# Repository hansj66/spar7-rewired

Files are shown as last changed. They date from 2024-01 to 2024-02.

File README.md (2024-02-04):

# Spar7 Rewired

This repository contains schematics, PCB layout, gerber files and STEP/STL files necessary for a complete Spar 7 rebuild.

 > **Disclaimer:** This repository contains information about my own rebuild. I can not guarantee that this will work as expected in YOUR game. It is entirely possible that you will break your beautiful collector quality game beyond repair trying to retrofit this board and the 3D printed hopper mechanism. Proceed at your own risk :)

Note: The payout slide is currently made of 1.7mm thick 3D printed plastic. This part will wear out over time, and the life expectancy of this part is currently unknown. A CNC fabricated aluminium/steel sheet with 3D printed endcaps is a better option if this is a concern.

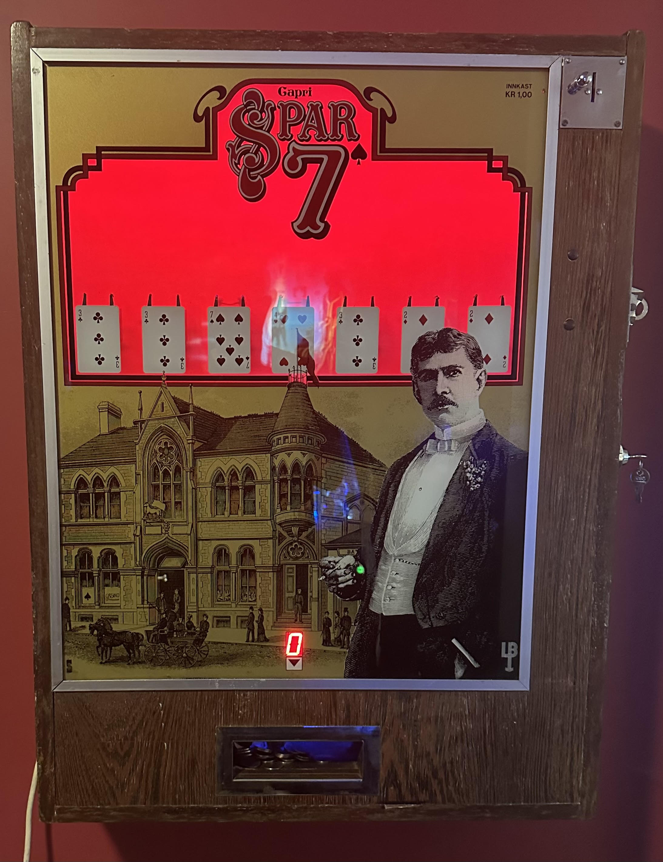
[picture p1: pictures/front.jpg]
Spar7

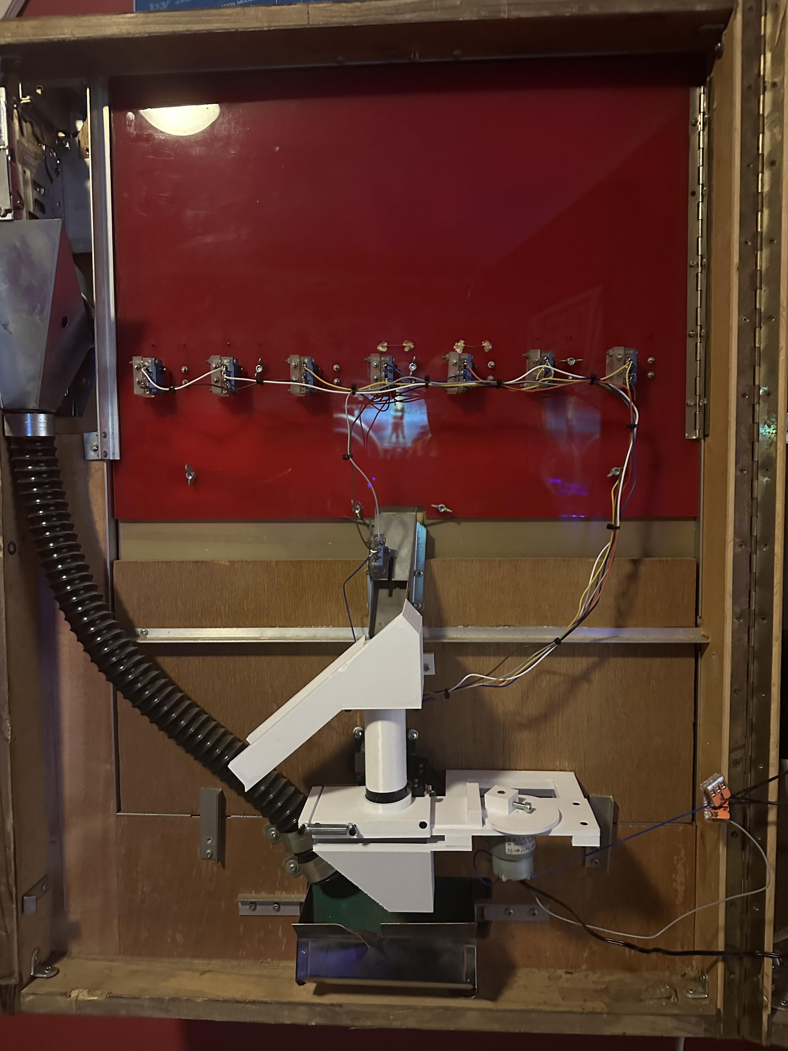
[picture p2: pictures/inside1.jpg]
Spar7_2

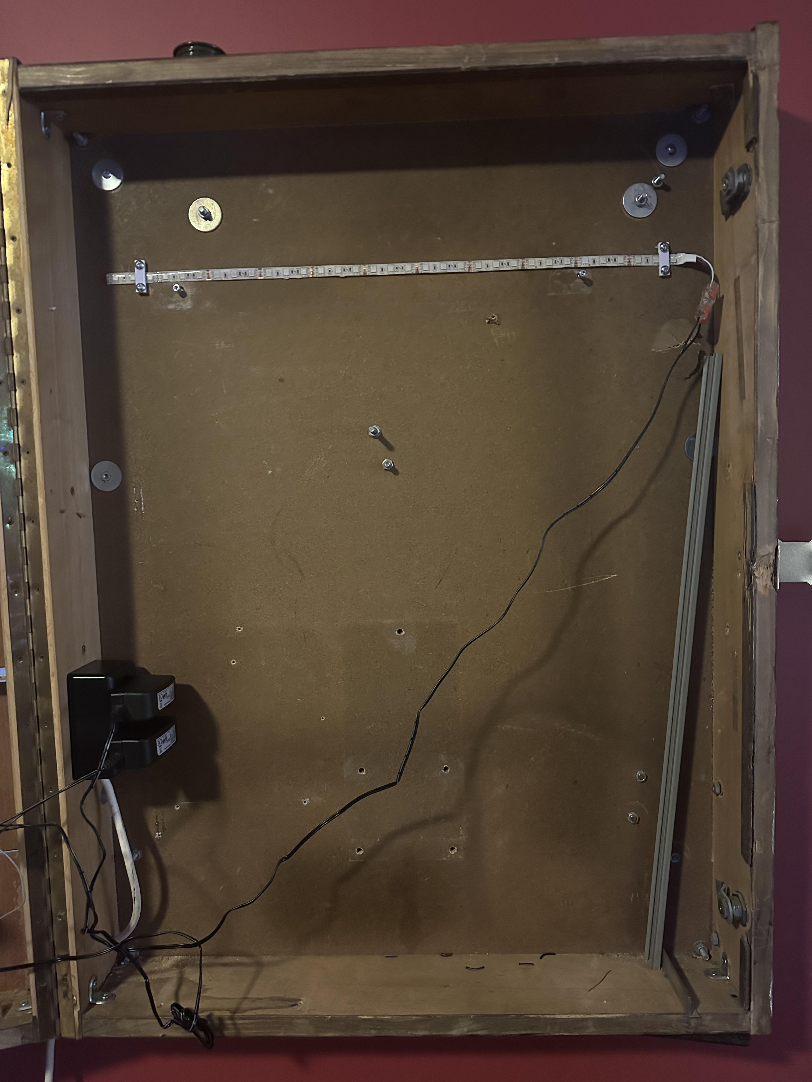
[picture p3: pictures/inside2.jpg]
Spar7_3


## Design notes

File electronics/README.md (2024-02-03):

# Eagle files

Here you will find a bill of materials along with eagle project files. Gerber files that can be uploaded to a PCB manufacturer can be found in the CAM folder

## Notes
1. There is no hardware debouncing in this version. A RC filter + schmitt trigger should be added to the inputs if you are planing on using interrupt handlers for the inputs.
2. The relay is rated for higher voltages than 12V, but I would not recommend using this for controlling a line voltage driven AC motor (220V can kill).
3. The 3.3V, 12V and USB leds are a bit on the bright side. Use series resistors with a higher resistance or consider not mounting these LEDs if light leakage to the payout slot is considered annoying.

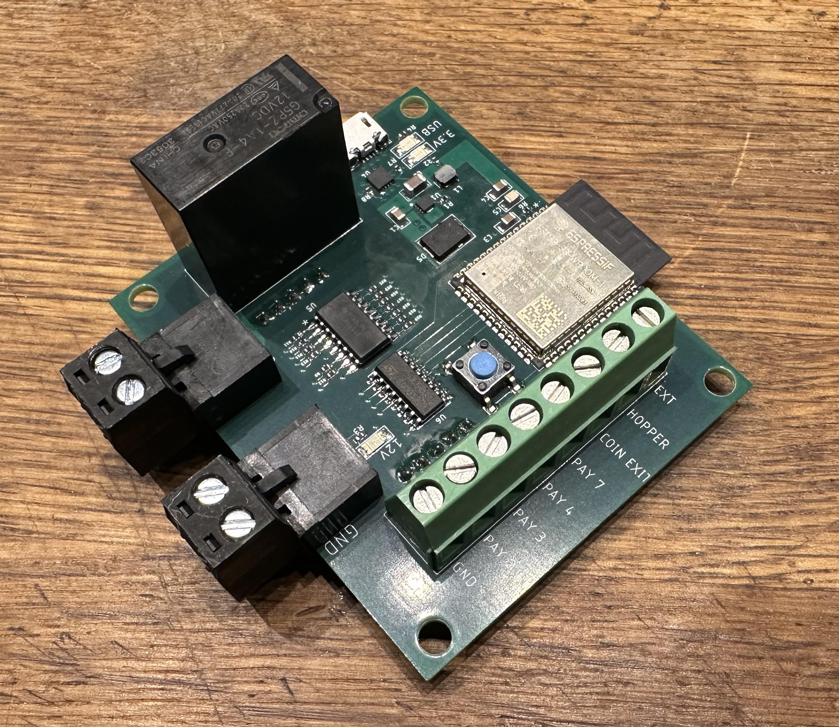
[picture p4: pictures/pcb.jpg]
pcb


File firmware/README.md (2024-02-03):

# Spar 7 Controller

## Building the firmware

1. Download [espressif installer ](https://dl.espressif.com/dl/esp-idf/?idf=4.4)
2. Configure environemnt variable IDF_PATH to point to espressif installation folder
3. If using visual studio code: Install the espressif plugin
4. Drop any certs into the certs/ folder. Any files dropped here will be packed into spiffs.bin if you run the makespiffs.cmd script. The spiffs.bin file will in turn automatically be flashed to the spiffs partition when you flash the firmware. This is required if you want to communicate using dtls over the wifi network.

```
idf.py build 
```

## Flashing

The board can be flashed using a USB Micro B cable. Press the blue button and apply power to the board to enter bootloader mode.

```
idf.py flash -p <port>
```

## Logging / shell

Log output and shell commands are available via USB. Type "Help" to get a list of commands.

```
idf.py monitor
```

## Shell commands

| Command  | Description |
| --- | --- |
| help  | Print the list of registered commands.  |
| free  | Get the current size of free heap memory.  |
| heap  | Get minimum size of free heap memory that was available during program execution.|
| version  | Get version of chip, SDK and firmware.  |
| restart | Software reset of the chip. |
| tasks  | Get information about running tasks. |
| log_level  \<tag\|\*\> \<none\|error\|warn\|debug\|verbose\>  |  Set log level for all tags or a specific tag. |
| get_delays  | Get information about current debounce / delay settings. |
| set_delay  <hopper\|exit\|payout> \<ms\>  |  Set debounce delay for a switch group (hopper, coin exit or payout) in milliseconds.|
| set_wifi \<ssid\> \<password\>  |  Set wifi ssid/password for your local network. (required for backend functionality). |
| ip  |  Get IP address. |
| dir  |  Lists files in filesystem. |
| txtest  |  Sends a hello world message to the backend. |

## Necessary hardware changes.

* Remove the internal lighting, power supply, hopper, printed circuit boards and associated wiring.
* 3D print all STL files in the "3D-print\STL" folder and assemble the new hopper (You will also need an assortment of 6mm, 15mm and 20mm M3 screws and 4 wood screws). The hopper is designed for a 12V JBG37-520 geared DC motor (60 or 120 RPM). If a motor with a different form factor is going to be used, you will have to import, modify and reslice the step files accordingly.
* Replace the existing fluorescent tube with a 12V LED strip. This can be powered from the same power supply as the motor.

> Note: The 7 segment display is optional. The board will work fine for games that don't have display option.

### 1. Switch wiring
* Remove (or modify) the existing wiring harness. If the switch terminal lugs are heavily oxidized, it may be a good idea to solder the wiring harness directly to the lugs instead of using connectors.
* Route a common switch ground wire through all payout switches, coin exit switch and hopper switch and connect this to the GND terminal on the 8 pin terminal block.
* Route all wires from the "2"-switches to the ""Pay 2" terminal, "3"-switches to the "Pay 3" etc. Also connect the "coin exit" and hopper switches to the corresponding terminals (The "Ext" terminal is currently not in use)

### 2. Motor wiring
1. Connect a 12V 1A power supply to the power pluggable terminal block.
1.  Connect the motor in series with a separate 12V power supply and connect the remaining wire going from the power supply and the remaning wire going from the motor to the "Motor Relay" pluggable terminal block.
1. In case the default debounce delays don't work for your setup, these delays can be changed using shell commands (the shell is always available via the USB.)

Example:

Changing the hopper debounce delay to 250ms:
```
set_delay hopper 250
```
## IoT Backend Notes

If you are using the [https://span.lab5e.com/](https://span.lab5e.com/) IoT backend, you will have to create a representation of your device and download the necessary certificates. (It's free to register and use for hobbyists level number of devices and data. You'll find all necessary information in the [Getting Started section](https://www.lab5e.com/docs/get_started/) of the documentation).

1. Create a folder under firmware (firmware\certs) and drop the <deviceid>-cert.crt, the <deviceid>-key.key and the span-cert-chain.crt in this folder
1. Concatenate <deviceid>-cert.crt and span-cert-chain.crt to a new 'cert.crt' file in the same folder (the device cert has to be the first certificate).

This folder will automatically be flashed to the spiffs partition when you flash the firmware. If you set the wifi ssid and password using the command shell, the firmware will try to connect to your wifi. If successful, bookkeeping data will then be sent when coins are received or paid out from the game using dtls.

The protocol is rather simple. Messages consist of one byte only. A positive number == coin in. A negative number == coins out. (I considered using protobuffers, but decided it would be overkill for now...)

The Span backend provides data retention. It also has a REST api and various outputs that make it simple to write a small application/backend to retrieve these messages from Span at your convenience. [Example clients](https://www.lab5e.com/docs/backend/) are available for a wide variety of languages.

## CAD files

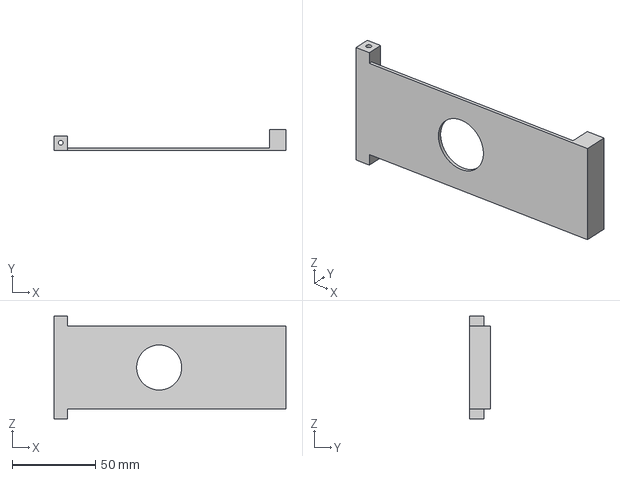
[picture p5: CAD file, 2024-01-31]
3D_print/step/slider.step
139.0 x 12.7 x 61.4 mm

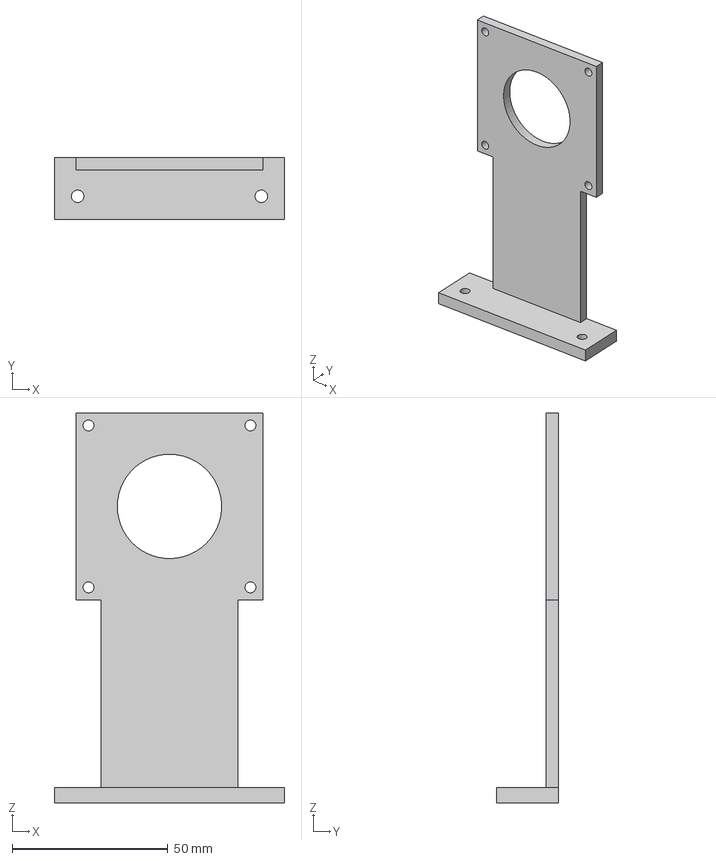
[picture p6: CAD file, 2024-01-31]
3D_print/step/tube bracket.step
74.0 x 20.0 x 125.2 mm

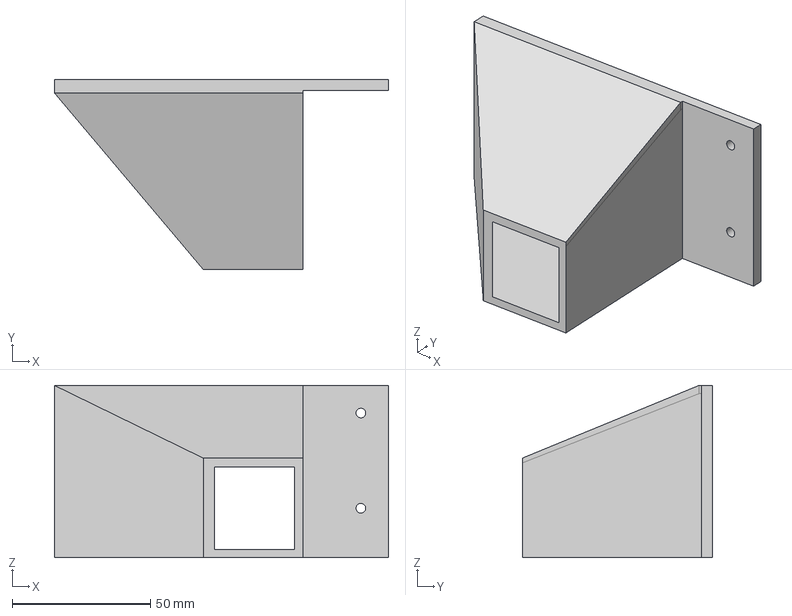
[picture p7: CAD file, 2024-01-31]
3D_print/step/funnel.step
121.0 x 69.0 x 62.3 mm

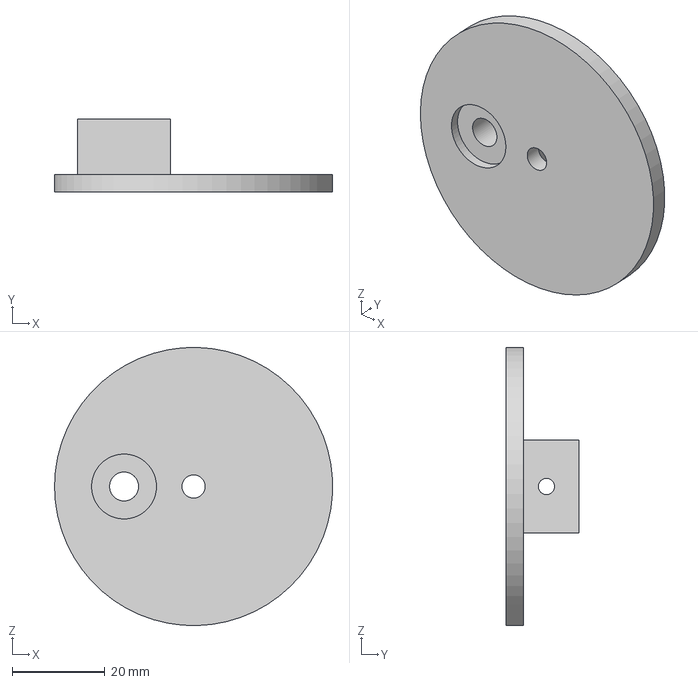
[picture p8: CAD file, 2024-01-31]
3D_print/step/rotor.step
60.0 x 15.7 x 60.0 mm

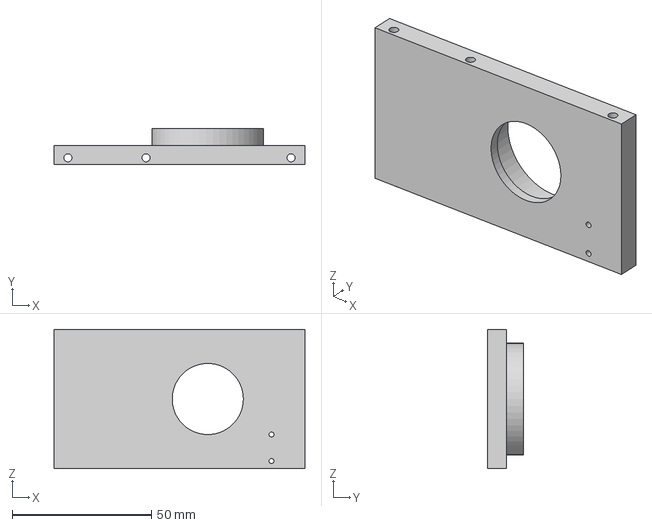
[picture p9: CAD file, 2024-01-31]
3D_print/step/top plate.step
90.0 x 12.9 x 50.0 mm

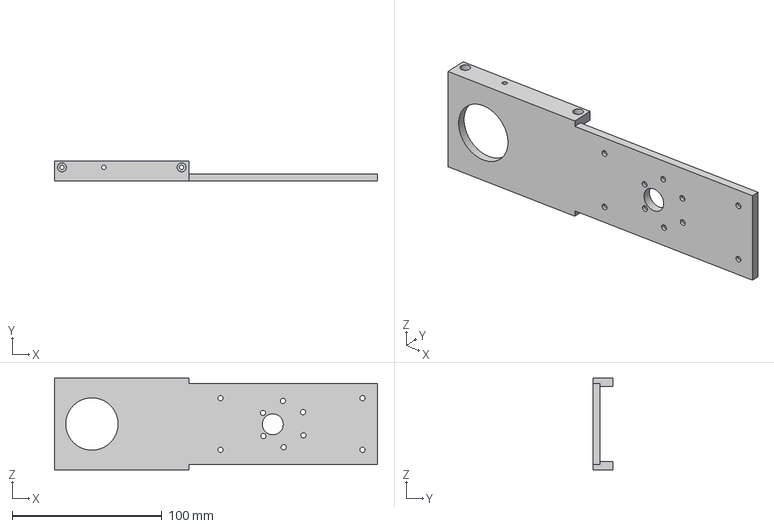
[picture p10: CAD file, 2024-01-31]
3D_print/step/bottom_plate.step
216.0 x 13.7 x 61.5 mm

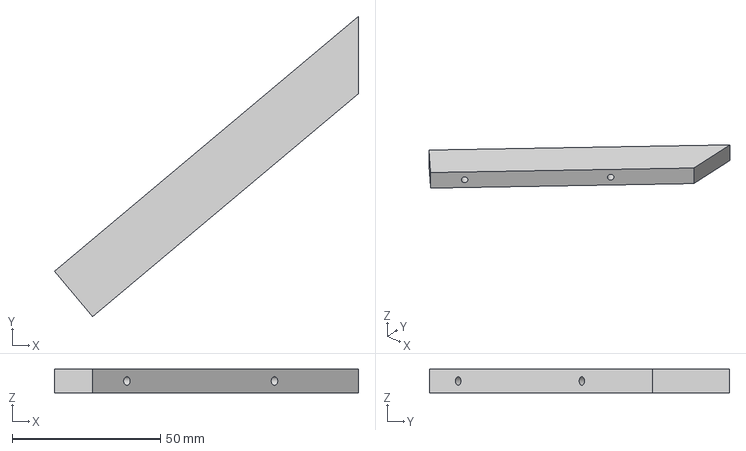
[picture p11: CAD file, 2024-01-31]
3D_print/step/coin chute_b.step
102.6 x 101.4 x 8.00 mm

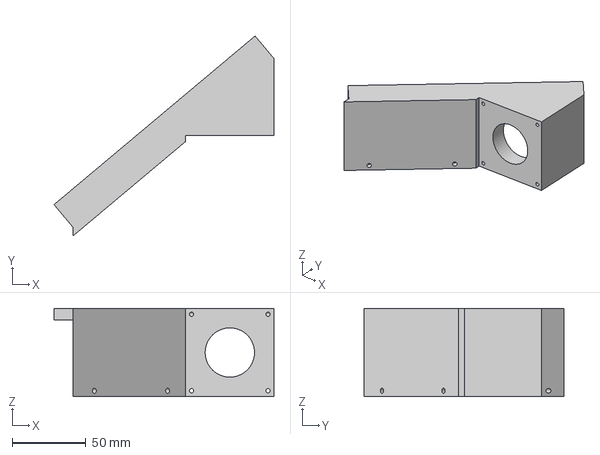
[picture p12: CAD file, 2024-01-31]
3D_print/step/coin chute_a.step
149.5 x 135.9 x 60.0 mm

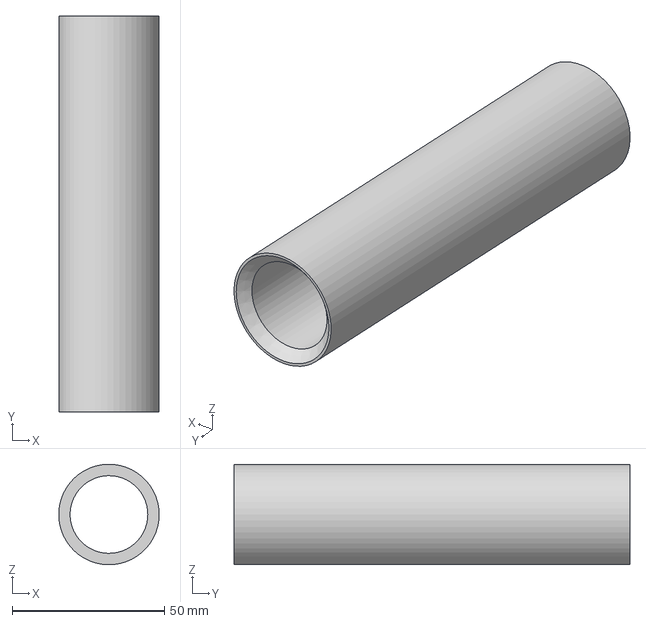
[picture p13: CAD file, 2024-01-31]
3D_print/step/coin tube.step
33.0 x 130.0 x 33.0 mm

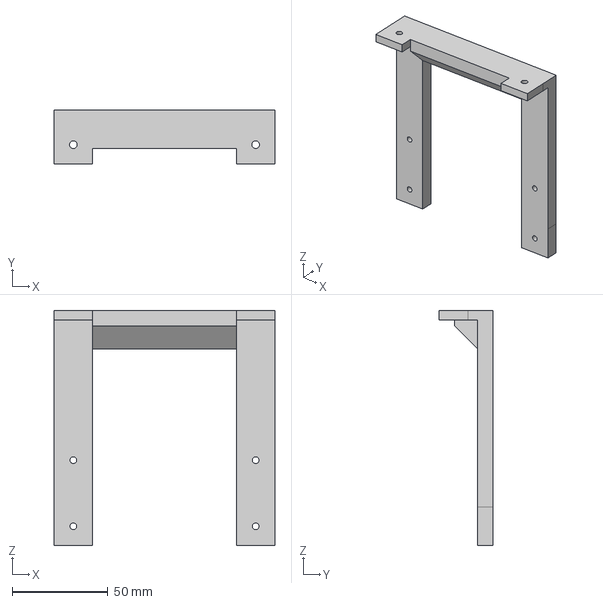
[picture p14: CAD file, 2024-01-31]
3D_print/step/bracket.step
115.0 x 28.0 x 122.5 mm

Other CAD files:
3D_print/fusion360/Hopper - Alternative version v18.f3d
3D_print/stl/Coin Tube.stl
3D_print/stl/Top plate.stl
3D_print/stl/Tube bracket.stl
3D_print/stl/bottom_plate.stl
3D_print/stl/bracket.stl
3D_print/stl/coin chute_a.stl
3D_print/stl/coin chute_b.stl
3D_print/stl/funnel.stl
3D_print/stl/rotor.stl
3D_print/stl/slider.stl

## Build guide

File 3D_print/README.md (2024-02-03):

# Spar 7 Alternative Hopper

Here you will find STL files for 3D printing the alternative hopper. STEP-files and a Fusion360 project export are also included (in case you would like to modify the design)

## Notes
1. 4 wooden screws are needed to mount the hopper to the inside plywood wall. Make sure to use short screws, so you don't penetrate the plywood and break the front glass ;)
2. The CAM is for a 6mm shaft motor. It is secured to the shaft using an M4 screw
3. Assembling thw hopper requires M3 6mm screws, M3 15 and 20mm screws
4. The payout slide requires two soft springs (approx 20mm in length)
5. The motor bracket is designed for a JGB37-500 motor. This can be sourced from AliExpress.

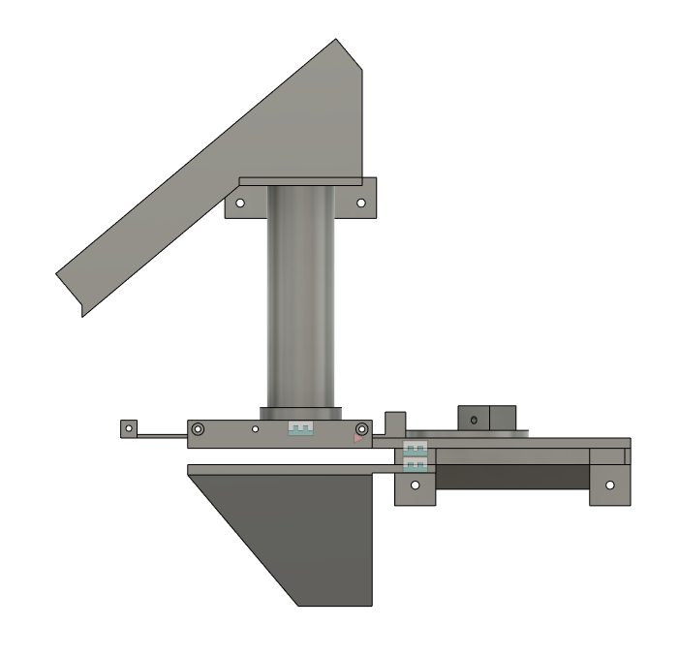
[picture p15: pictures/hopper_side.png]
hopper side

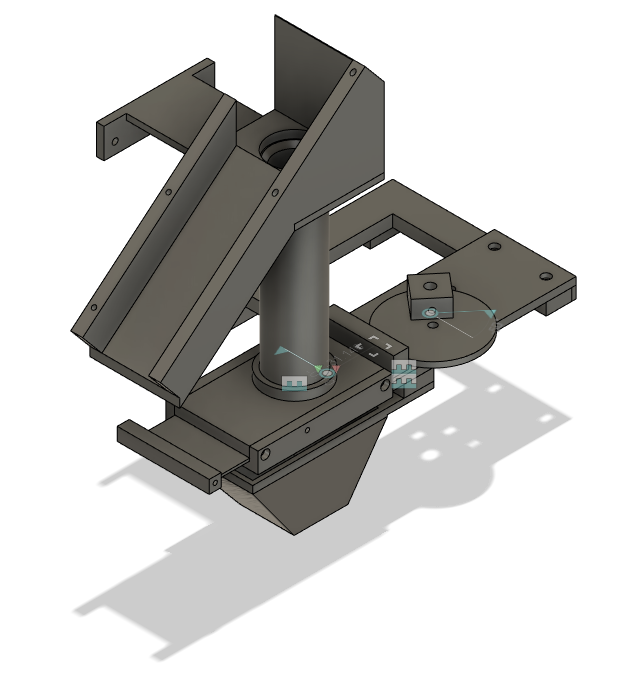
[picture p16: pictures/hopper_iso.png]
hopper iso


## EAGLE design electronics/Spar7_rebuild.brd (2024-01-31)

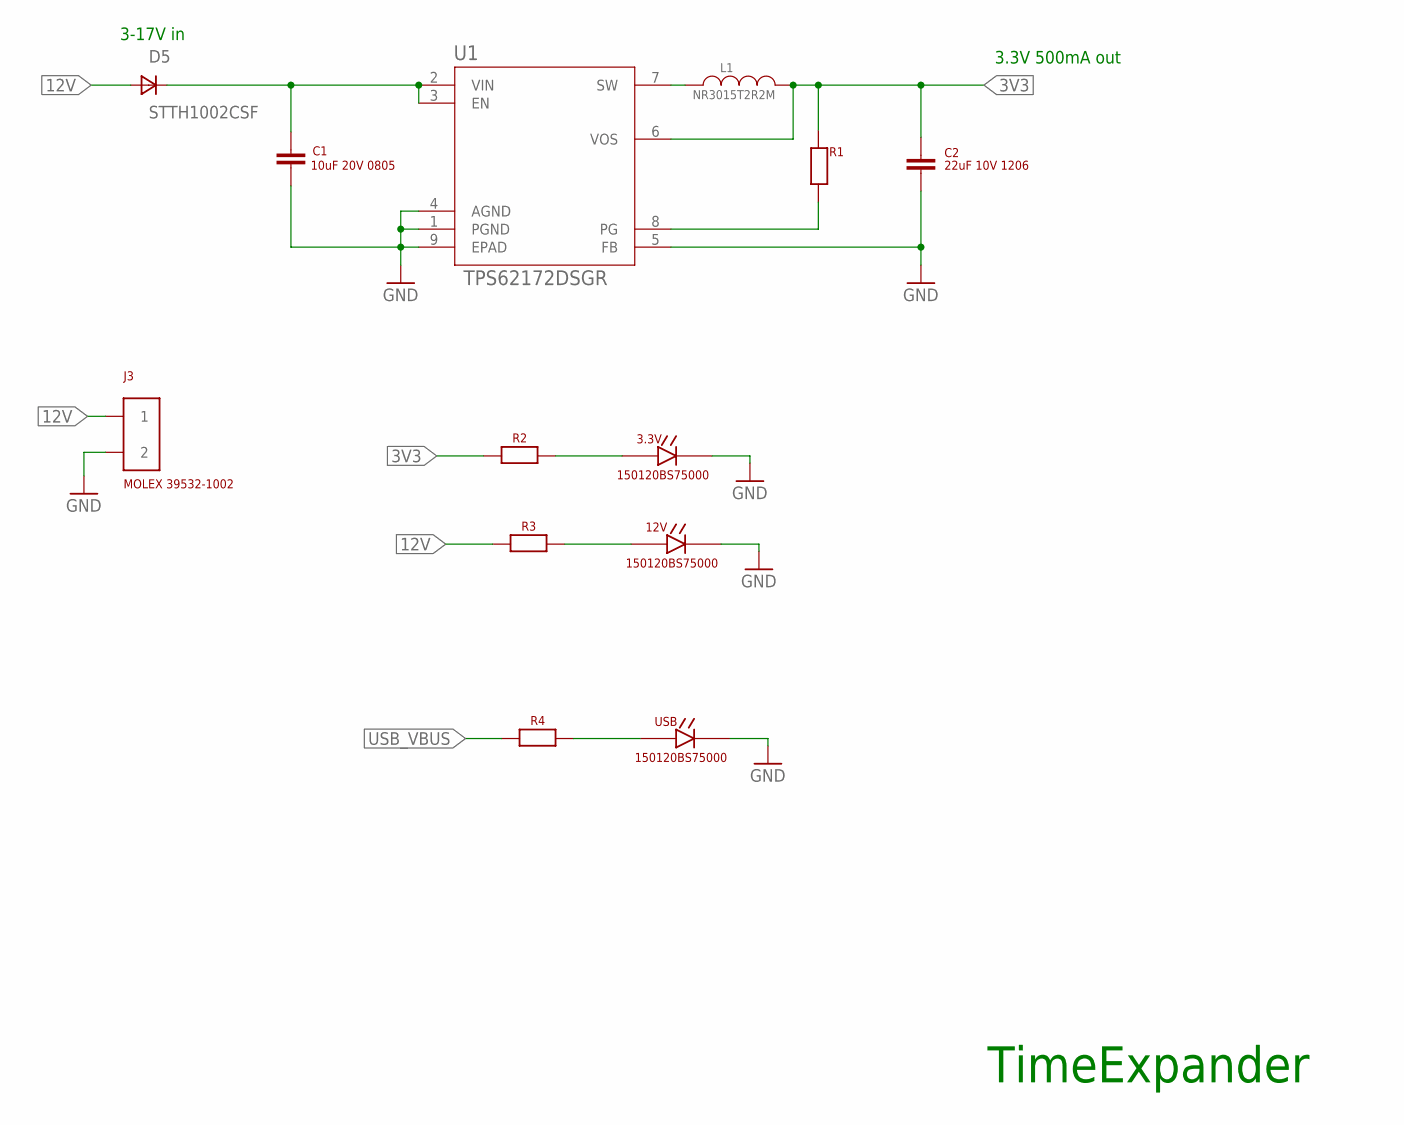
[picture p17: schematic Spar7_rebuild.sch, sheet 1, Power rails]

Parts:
3.3V, 12V: 150120BS75000
C1: 10uF 20V 0805; CAP_0805
C2: 22uF 10V 1206; CAP_1206
D5: STTH1002CSF; DIODE_STTH1002CSF
J3: MOLEX-39532-1002
L1: NR3015T2R2M; IND_TAIYO_NR3015_TAY
R1, R2, R3, R4: RESISTOR0402; RES_0402
U1: TPS62172DSGR; DSG8_1P6X0P9
USB: 150120BS75000

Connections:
3V3: C2.P$1 (1), L1.1, R1.P$1, R2.P$1, U1.6 (VOS); also elsewhere on the board
12V: D5.A1 (A), D5.A2 (A), J3.1, R3.P$1; also elsewhere on the board
GND: 3.3V.C, 12V.C, C1.P$2 (2), C2.P$2 (2), J3.2, U1.1 (PGND), U1.4 (AGND), U1.5 (FB), U1.9 (EPAD), USB.C; also elsewhere on the board
unnamed: L1.2, U1.7 (SW)
unnamed: 12V.A, R3.P$2
unnamed: R1.P$2, U1.8 (PG)
unnamed: R4.P$2, USB.A
unnamed: 3.3V.A, R2.P$2
unnamed: C1.P$1 (1), D5.C, U1.2 (VIN), U1.3 (EN)
USB_VBUS: R4.P$1; also elsewhere on the board

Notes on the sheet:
3.3V 500mA out
3-17V in
TimeExpander

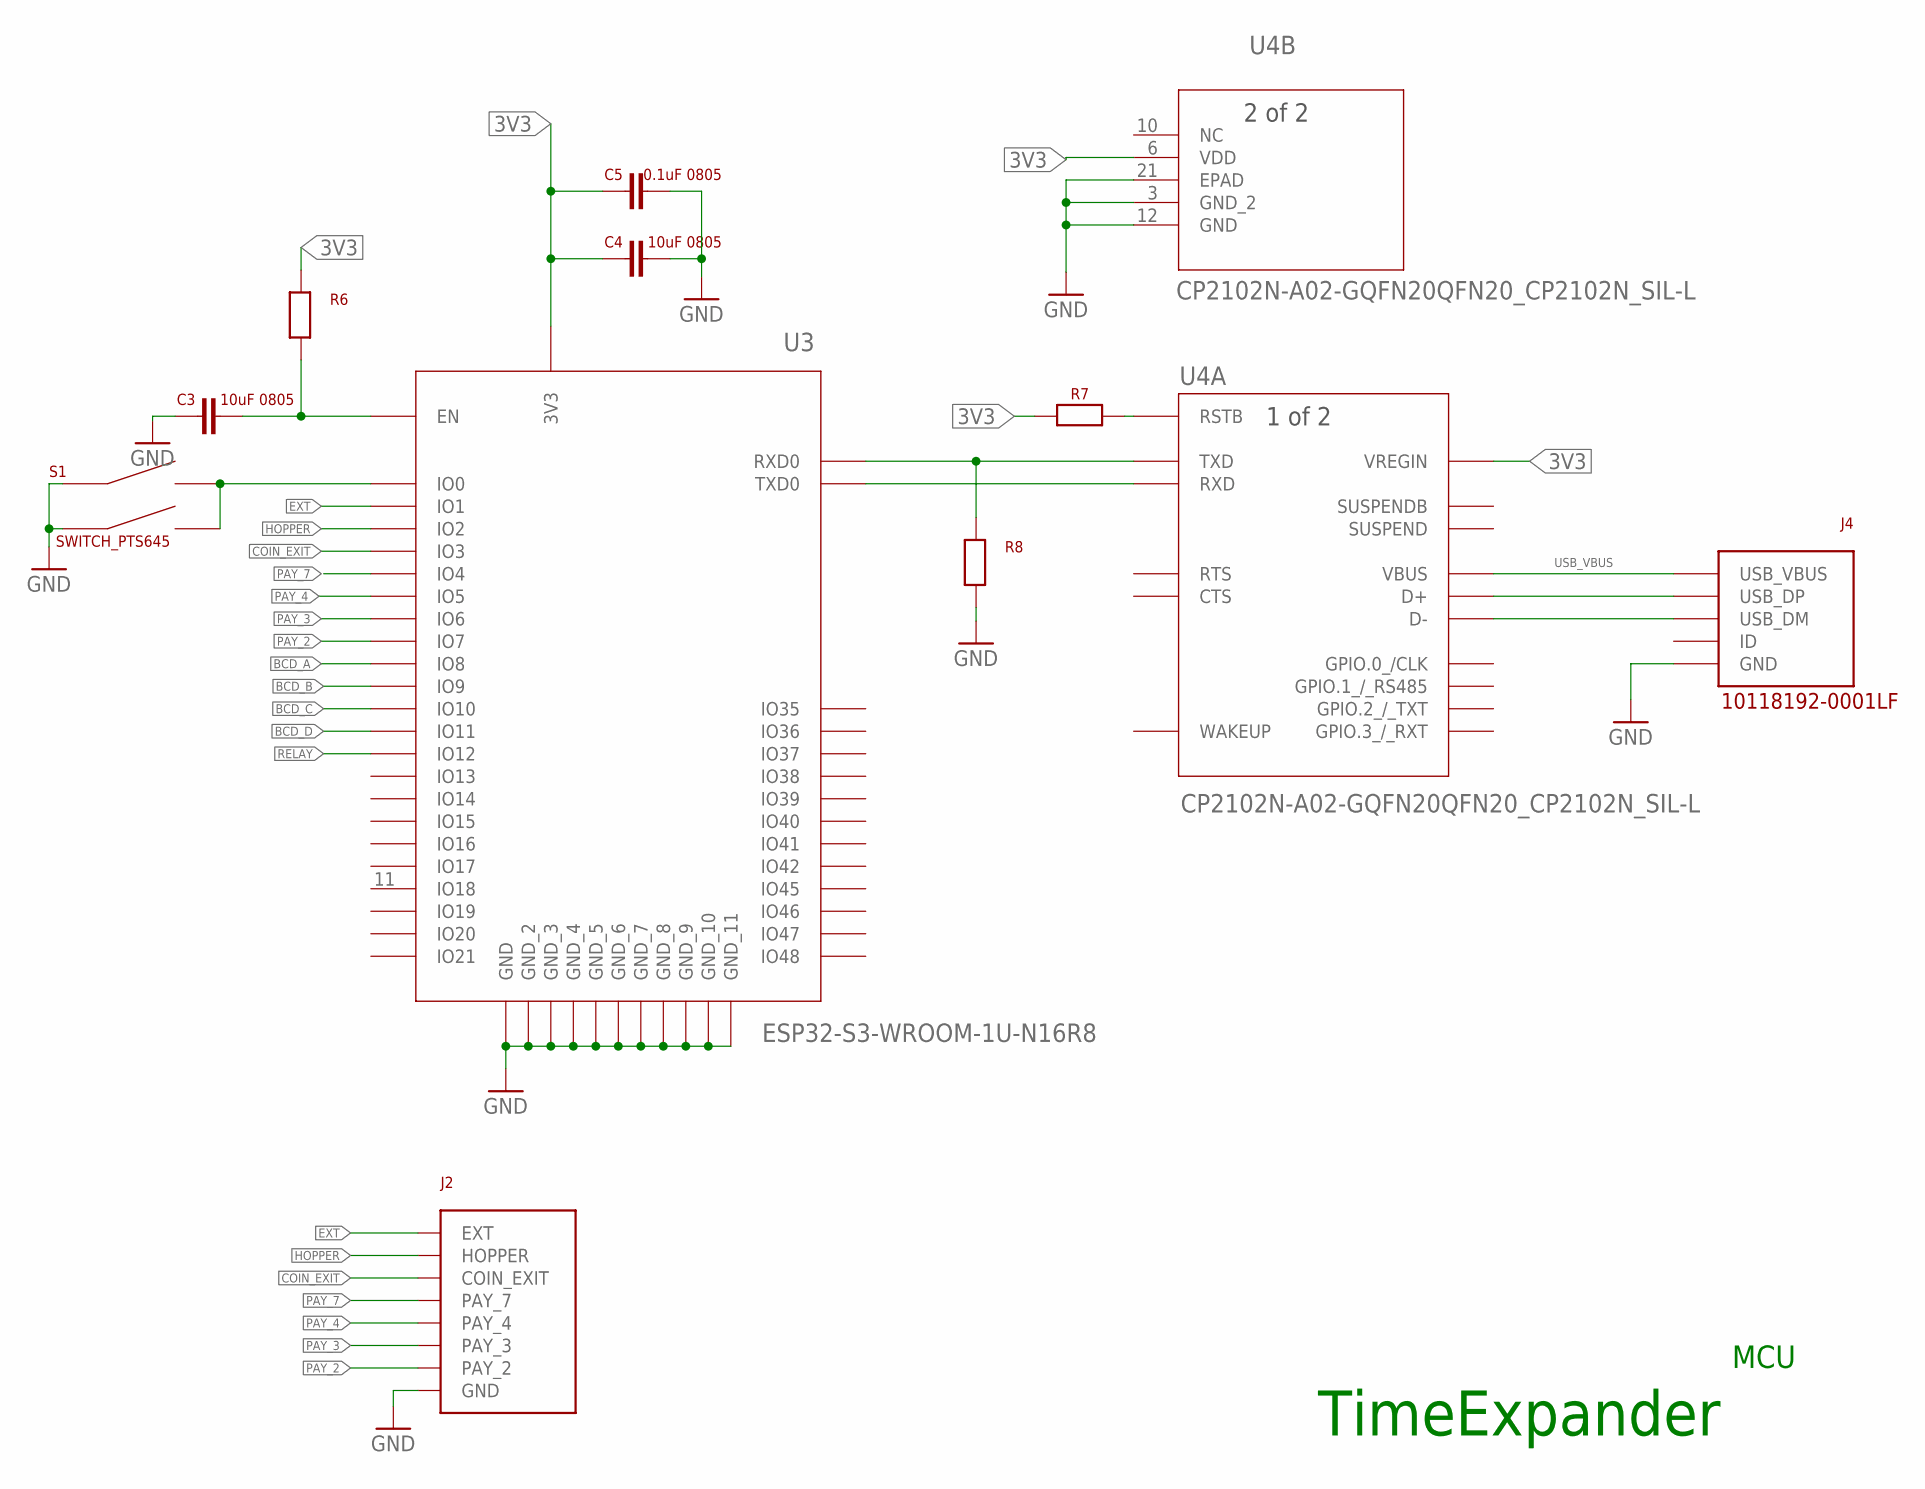
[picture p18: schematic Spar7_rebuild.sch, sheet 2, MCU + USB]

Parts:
C3, C4: 10uF 0805; CAP_0805
C5: 0.1uF 0805; CAP_0805
J2: SPAR7_REWIRED_TERM_BLOCK
J4: 10118192-0001LF; USB_RCPT_10118192-0001LF
R6, R7, R8: RESISTOR0402; RES_0402
S1: SWITCH_PTS645; SWITCH_PTS645_EE_NBIOT_01
U3: ESP32-S3-WROOM-1U-N16R8; ESP32­S3­WROOM­1U_EXP
U4: CP2102N-A02-GQFN20QFN20_CP2102N_SIL-L; QFN20_CP2102N_SIL-L

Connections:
3V3: C4.P$1 (1), C5.P$1 (1), R6.P$2, R7.P$1, U3.2 (3V3), U4.6 (VDD), U4.7 (VREGIN); also elsewhere on the board
BCD_A: U3.12 (IO8); also elsewhere on the board
BCD_B: U3.17 (IO9); also elsewhere on the board
BCD_C: U3.18 (IO10); also elsewhere on the board
BCD_D: U3.19 (IO11); also elsewhere on the board
COIN_EXIT: J2.COIN_EXIT, U3.15 (IO3)
EXT: J2.EXT, U3.39 (IO1)
GND: C3.P$1 (1), C4.P$2 (2), C5.P$2 (2), J2.GND, J4.GND, R8.P$1, S1.A1, S1.A2, U3.1 (GND_2), U3.40 (GND_3), U3.41 (GND_4), U3.42 (GND_5), U3.43 (GND_6), U3.44 (GND_7), U3.45 (GND_8), U3.46 (GND_9), U3.47 (GND_10), U3.48 (GND_11), U3.49 (GND), U4.3 (GND_2), U4.12 (GND), U4.21 (EPAD); also elsewhere on the board
HOPPER: J2.HOPPER, U3.38 (IO2)
unnamed: J4.D+ (USB_DP), U4.4 (D+)
unnamed: J4.D- (USB_DM), U4.5 (D-)
unnamed: R7.P$2, U4.9 (RSTB)
unnamed: R8.P$2, U3.36 (RXD0), U4.18 (TXD)
unnamed: U3.37 (TXD0), U4.17 (RXD)
unnamed: S1.B1, S1.B2, U3.27 (IO0)
unnamed: C3.P$2 (2), R6.P$1, U3.3 (EN)
PAY_2: J2.PAY_2, U3.7 (IO7)
PAY_3: J2.PAY_3, U3.6 (IO6)
PAY_4: J2.PAY_4, U3.5 (IO5)
PAY_7: J2.PAY_7, U3.4 (IO4)
RELAY: U3.20 (IO12); also elsewhere on the board
USB_VBUS: J4.VCC (USB_VBUS), U4.8 (VBUS); also elsewhere on the board

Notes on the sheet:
TimeExpander
MCU

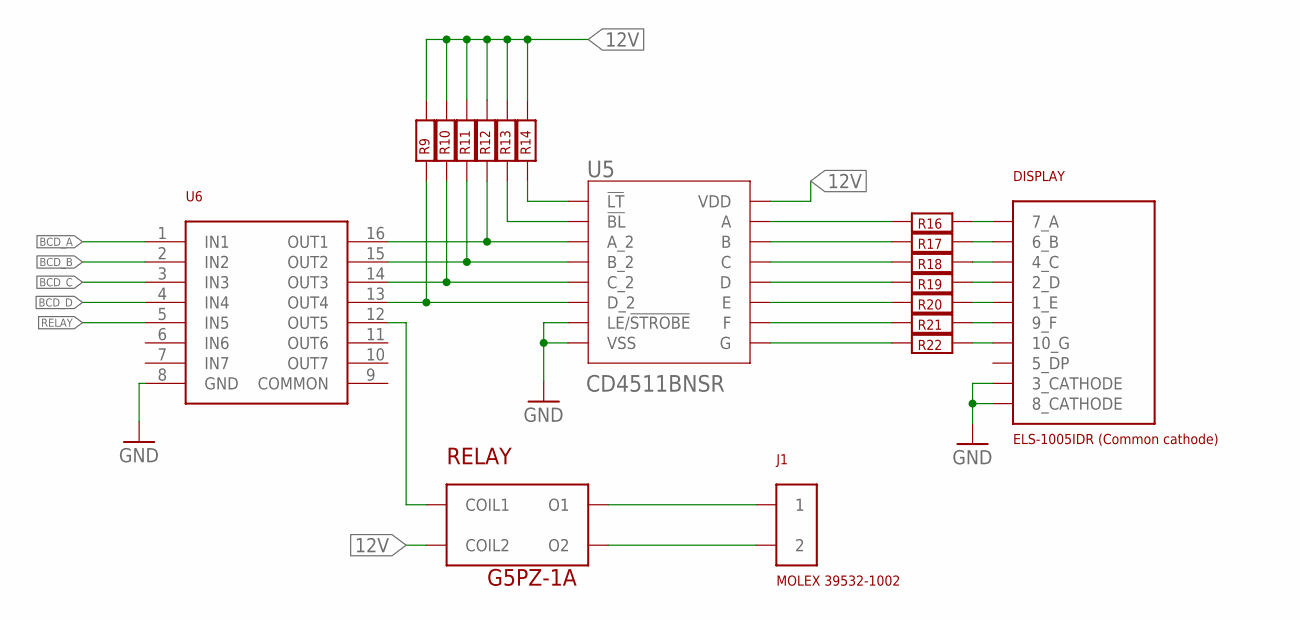
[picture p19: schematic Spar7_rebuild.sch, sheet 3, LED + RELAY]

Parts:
DISPLAY: ELS-1005IDR-SA10-21EWA
J1: MOLEX-39532-1002
R9, R10, R11, R12, R13, R14, R16, R17, R18, R19, R20, R21, R22: RESISTOR0402; RES_0402
RELAY: G5PZ-1A_RELAY
U5: CD4511BNSR; NS16
U6: ULN2003D1013TR; SO16-NARROW

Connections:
12V: R9.P$2, R10.P$2, R11.P$2, R12.P$2, R13.P$2, R14.P$2, RELAY.COIL2, U5.16 (VDD); also elsewhere on the board
BCD_A: U6.1 (IN1); also elsewhere on the board
BCD_B: U6.2 (IN2); also elsewhere on the board
BCD_C: U6.3 (IN3); also elsewhere on the board
BCD_D: U6.4 (IN4); also elsewhere on the board
GND: DISPLAY.3_CATHODE, DISPLAY.8_CATHODE, U5.5 (LE/!STROBE), U5.8 (VSS), U6.8 (GND); also elsewhere on the board
unnamed: J1.1, RELAY.O1
unnamed: DISPLAY.7_A, R16.P$1
unnamed: DISPLAY.6_B, R17.P$1
unnamed: DISPLAY.4_C, R18.P$1
unnamed: DISPLAY.2_D, R19.P$1
unnamed: DISPLAY.1_E, R20.P$1
unnamed: DISPLAY.9_F, R21.P$1
unnamed: DISPLAY.10_G, R22.P$1
unnamed: R16.P$2, U5.13 (A)
unnamed: R17.P$2, U5.12 (B)
unnamed: R18.P$2, U5.11 (C)
unnamed: R19.P$2, U5.10 (D)
unnamed: R20.P$2, U5.9 (E)
unnamed: R21.P$2, U5.15 (F)
unnamed: R22.P$2, U5.14 (G)
unnamed: R14.P$1, U5.3 (!LT)
unnamed: R13.P$1, U5.4 (!BL)
unnamed: R12.P$1, U5.7 (A_2), U6.16 (OUT1)
unnamed: R11.P$1, U5.1 (B_2), U6.15 (OUT2)
unnamed: R10.P$1, U5.2 (C_2), U6.14 (OUT3)
unnamed: R9.P$1, U5.6 (D_2), U6.13 (OUT4)
unnamed: RELAY.COIL1, U6.12 (OUT5)
unnamed: J1.2, RELAY.O2
RELAY: U6.5 (IN5); also elsewhere on the board

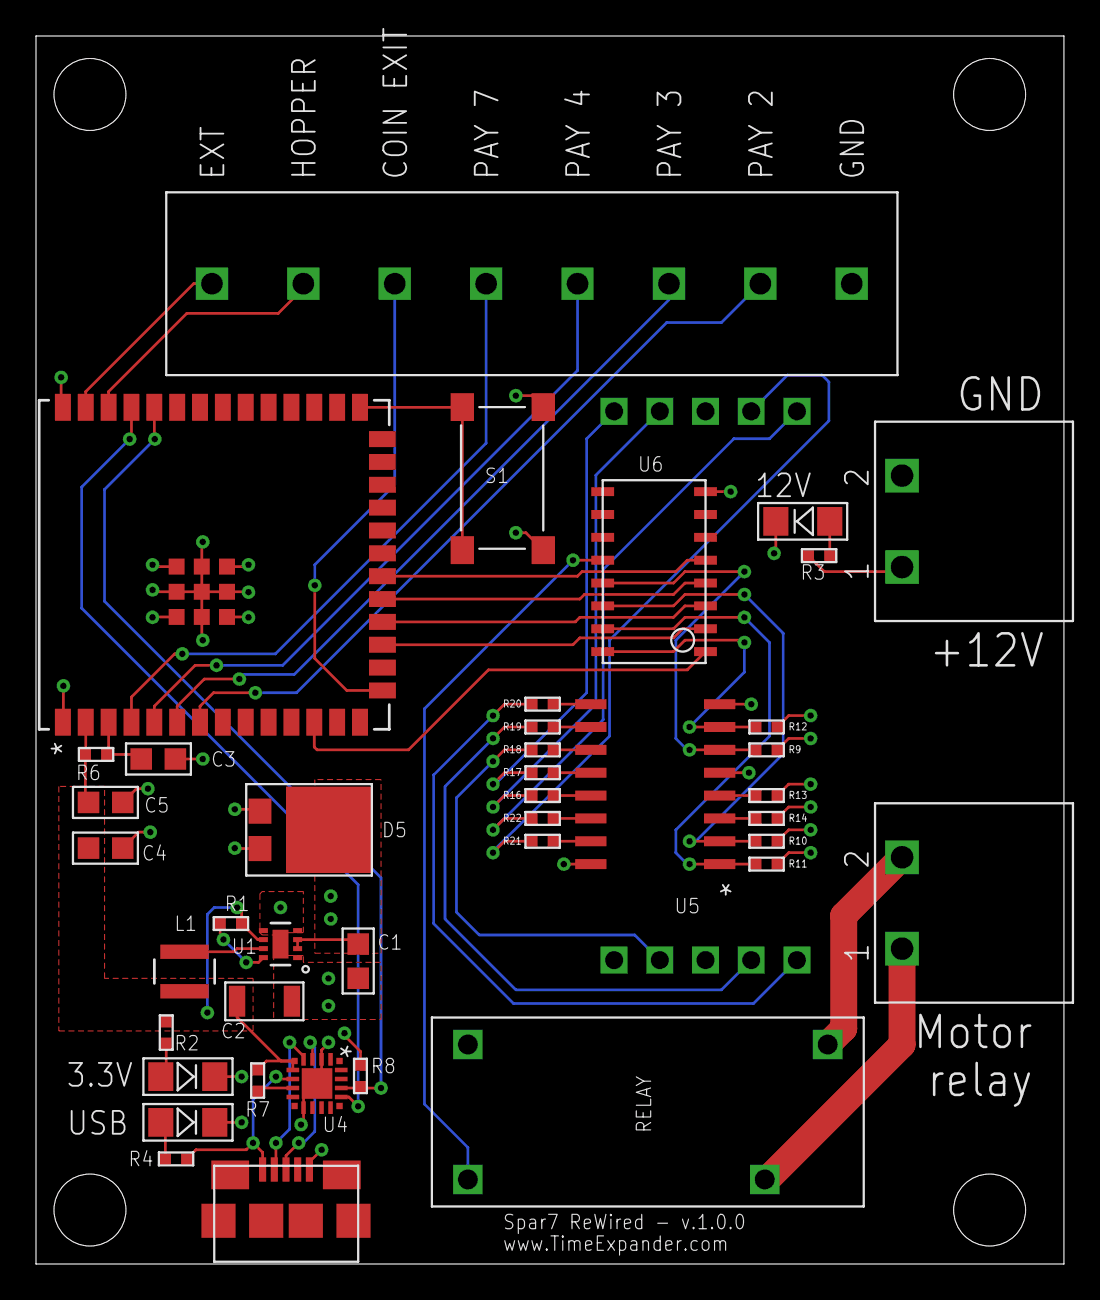
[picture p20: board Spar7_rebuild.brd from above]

Board: 4 copper layers, 57.1 x 68.2 mm, 42 parts (1 on the bottom side), 52 nets.

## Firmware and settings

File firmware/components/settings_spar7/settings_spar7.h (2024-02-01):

#ifndef _SETTINGS_SPAR7_H_
#define _SETTINGS_SPAR7_H_

#include <stddef.h>

#define SSID_MAX_LENGTH 50
#define PASSWORD_MAX_LENGTH 50

#define DEFAULT_PAYOUT_DELAY_MS     10
#define DEFAULT_COIN_EXIT_DELAY_MS  10
#define DEFAULT_HOPPER_DELAY_MS     300

typedef enum
{
    PAYOUT_DEBOUNCE = 0,
    COIN_EXIT_DEBOUNCE,
    HOPPER_DEBOUNCE,
} setting_t;

void set_debounce(setting_t s, int value);
int get_debounce(setting_t s);
void set_wifi(const char * ssid, const char * password);
void get_wifi_ssid(char * ssid, size_t* length);
void get_wifi_password(char * password, size_t* length);

#endif

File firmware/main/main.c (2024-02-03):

// Copyright 2024 Hans Jørgen Grimstad

// Licensed under the Apache License, Version 2.0 (the "License"); you may not use 
// this file except in compliance with the License. You may obtain a copy of the 
// License at http://www.apache.org/licenses/LICENSE-2.0 Unless required by applicable 
// law or agreed to in writing, software distributed under the License is distributed 
// on an "AS IS" BASIS, WITHOUT WARRANTIES OR CONDITIONS OF ANY KIND, either express or implied. 
// See the License for the specific language governing permissions and limitations under the License.

#include <stdio.h>
#include <inttypes.h>
#include "sdkconfig.h"
#include "freertos/FreeRTOS.h"
#include "freertos/queue.h"
#include "freertos/task.h"
#include "esp_chip_info.h"
#include "esp_flash.h"
#include "esp_system.h"
#include "sys/time.h"
#include "filesystem.h"
#include "esp_log.h"
#include "soc/soc.h"
#include "soc/gpio_reg.h"
#include "console.h"
#include "nvs.h"
#include "nvs_flash.h"
#include "settings_spar7.h"
#include "hal_spar7.h"
#include "wifi.h"
#include "dtls.h"

const uint8_t FIRMWARE_VERSION_MAJOR = 1;
const uint8_t FIRMWARE_VERSION_MINOR = 0;

#define HOST "data.lab5e.com"
#define PORT "1234"

static const char* TAG = "SPAR7";

extern int PAYOUT_DELAY_MS;
extern int COIN_EXIT_DELAY_MS;
extern int HOPPER_DELAY_MS;

// Task priorities (higher numbers == higher priorities)
//
#define CONSOLE_TASK_PRIORITY 10
#define GAME_TASK_PRIORITY 10
#define SEND_TASK_PRIORITY 20
// Max queue sizes
#define MAX_COIN_QUEUE_SIZE 20


void send_bookkeeping_data(int8_t data);

// Bookkeeping
//
int total_coins_in = 0;
int total_coins_out = 0;

// Queues
//
static QueueHandle_t coin_evt_queue = NULL;

void read_debounce_settings_from_nvs()
{
    get_debounce(PAYOUT_DEBOUNCE);
    get_debounce(COIN_EXIT_DEBOUNCE);
    get_debounce(HOPPER_DEBOUNCE);
}

static void console_task(void * arg)
{
    run_console();
}

static void game_task(void * arg)
{
    // Initialize display
    display_digit(0);

    uint32_t regs = REG_READ(GPIO_IN_REG);
    while  ((1ULL << GPIO_HOPPER) & ~regs)
    {
        regs = REG_READ(GPIO_IN_REG);
        start_motor();
    }
    stop_motor();

    
    while (true)
    {
        uint32_t regs = REG_READ(GPIO_IN_REG);

        int8_t payout = 0;

        if  ((1ULL << GPIO_PAY2) & ~regs)
            payout = 2;
        if  ((1ULL << GPIO_PAY3) & ~regs)
            payout = 3;
        if  ((1ULL << GPIO_PAY4) & ~regs)
            payout = 4;
        if  ((1ULL << GPIO_PAY7) & ~regs)
            payout = 7;
        if  ((1ULL << GPIO_COIN_EXIT) & ~regs)
        {
            // TODO: send message: coins in + 1 
        }

        if  (payout != 0)
        {
            printf("Payout: %d\n", payout);
            int countdown = payout;
            display_digit(countdown);

            send_bookkeeping_data(-payout);
            
            // Wait for coin exit
            for (;;)
            {
                regs = REG_READ(GPIO_IN_REG);
                if  ((1ULL << GPIO_COIN_EXIT) & ~regs)
                {
                    send_bookkeeping_data((int8_t)1);
                    printf("Coin exit\n");
                    break;
                }
                vTaskDelay(COIN_EXIT_DELAY_MS / portTICK_PERIOD_MS);
            }
      
            // Do payout
            start_motor();
            for (int i=0; i<payout; i++)
            {
                for (;;) 
                {
                    // wait for hopper
                    regs = REG_READ(GPIO_IN_REG);
                    if  ((1ULL << GPIO_HOPPER) & ~regs)
                    {
                        // Increment earnings by 1
                        printf("Hopper\n");

                        // Only debounce first n-1 coins
                        if (countdown >= 1)
                        {
                            vTaskDelay(HOPPER_DELAY_MS / portTICK_PERIOD_MS);
                        }
                       
                        countdown--;
                        display_digit(countdown);

                        if (countdown == 0)
                        {
                            break;
                        }
                    }
                    if (countdown == 0)
                    {
                        break;
                    }
                    vTaskDelay(1 / portTICK_PERIOD_MS);
                }

            }

            // Run motor until switch opens again
            regs = REG_READ(GPIO_IN_REG);
            while  ((1ULL << GPIO_HOPPER) & ~regs)
            {
                regs = REG_READ(GPIO_IN_REG);
            }
            vTaskDelay(10 / portTICK_PERIOD_MS);
            stop_motor();            
        }

        vTaskDelay(PAYOUT_DELAY_MS / portTICK_PERIOD_MS);
    }
}

void send_bookkeeping_data(int8_t data)
{
    if (is_wifi_online())
    {
        ESP_LOGI(TAG, "Sending bookkeeping data.");
        xQueueSend(coin_evt_queue, &data,  pdMS_TO_TICKS(1000));
    }
    else
    {
        ESP_LOGI(TAG, "Unable to send bookkeeping data (offline)");
    }
}


static void send_task(void * arg)
{
    // Block until we're online and ready to sedn bookkeeping data
    while (!is_wifi_online())
    {
        vTaskDelay(10 / portTICK_PERIOD_MS);
    }

     dtls_state_t dtls;

    if (!dtls_connect(&dtls, HOST, PORT)) 
    {
        dtls_close(&dtls);
    }
  
    printf("Connected to %s:%s\n", HOST, PORT);

   while (true)
    {
        int8_t data = 0;
        if (pdTRUE == xQueueReceive(coin_evt_queue, &data, portMAX_DELAY))
        {
            if (!dtls_send(&dtls, &data, 1)) 
            {
                ESP_LOGE(TAG, "Failed to send bookkeeping data.");
            }
            ESP_LOGI(TAG, "Sent message %02X", data);
        }
    }

    dtls_close(&dtls);  // Probably not happening anytome soon...
    printf("Closed connection\n");
}


static void initialize_nvs(void)
{
    esp_err_t err = nvs_flash_init();
    if (err == ESP_ERR_NVS_NO_FREE_PAGES || err == ESP_ERR_NVS_NEW_VERSION_FOUND) {
        ESP_ERROR_CHECK( nvs_flash_erase() );
        err = nvs_flash_init();
    }
    ESP_ERROR_CHECK(err);
}


void app_main(void)
{
    // Initialize NVS
    initialize_nvs();
    // Get delay settings
    read_debounce_settings_from_nvs();
    // Connect to wifi (if we have the credentials stored in NVS)
    wifi_connect();
    // Ini tialize GPIO
    init_gpio();
    // Initialize file system
    initialize_spiffs();

    // Create a queue to handle coin events
    coin_evt_queue =  xQueueCreate(MAX_COIN_QUEUE_SIZE, sizeof(int8_t));

    // start console task
    xTaskCreate(console_task, "Console Task", 8192, NULL, CONSOLE_TASK_PRIORITY, NULL);
    // start game task
    xTaskCreate(game_task, "Game Task", 4096, NULL, GAME_TASK_PRIORITY, NULL);
    // start send task
    xTaskCreate(send_task, "Send Task", 8192, NULL, SEND_TASK_PRIORITY, NULL);

    while (true)
    {
        vTaskDelay(10 / portTICK_PERIOD_MS);
    }
}

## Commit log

2024-01-04 added brd + sch
    [Spar7_rebuild.brd, Spar7_rebuild.sch]
2024-01-04 added BoM
2024-01-08 Added Spiffs partition
    * Added script for generating spiffs image from certs\chain
    * Added automatic flashing of spiffs image
    [partitions.csv]
2024-02-03 Fixed wifi
    * fixed display bug
    [hal_spar7.c, hal_spar7.h, main.c]

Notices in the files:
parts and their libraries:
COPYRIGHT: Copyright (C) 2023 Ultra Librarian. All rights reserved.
